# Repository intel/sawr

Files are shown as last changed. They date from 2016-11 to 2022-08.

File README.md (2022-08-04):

DISCONTINUATION OF PROJECT.

This project will no longer be maintained by Intel.

Intel has ceased development and contributions including, but not limited to, maintenance, bug fixes, new releases, or updates, to this project. 

Intel no longer accepts patches to this project.

If you have an ongoing need to use this project, are interested in independently developing it, or would like to maintain patches for the open source software community, please create your own fork of this project. 
Simple Autonomous Wheeled Robot (SAWR)
======================================

The goal of the SAWR project is to define a basic "example robot" to
demonstrate autonomous navigation using [ROS](http://wiki.ros.org/) with
the [Intel&reg; RealSense&trade; 3D cameras][RS]. This robot can also be
used as a software development and testing platform and to deliver training
material.

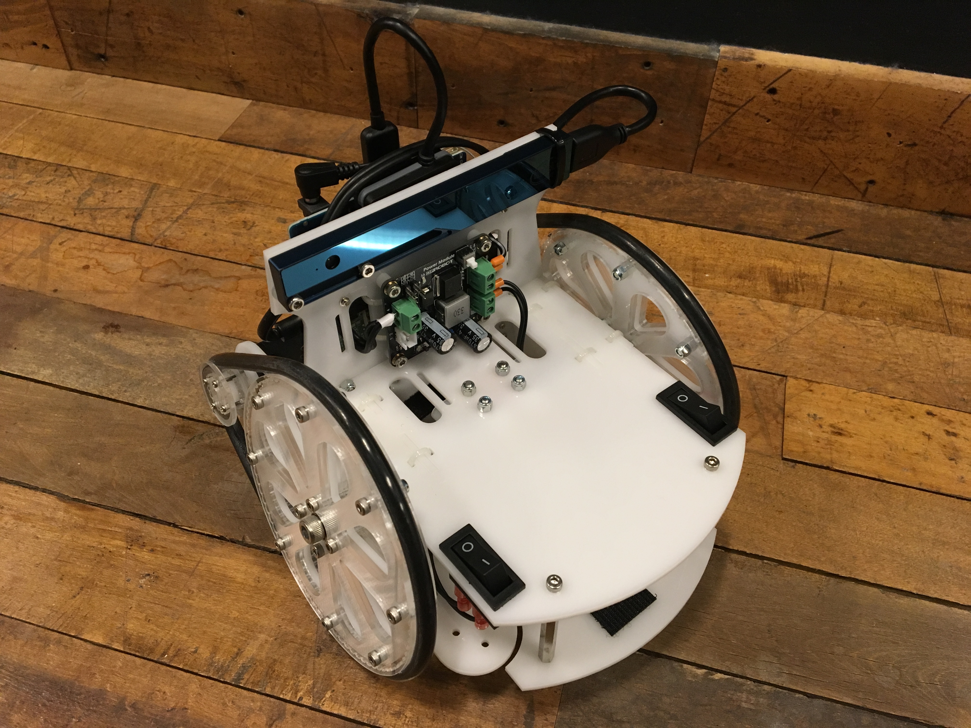
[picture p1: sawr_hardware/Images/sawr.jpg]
SAWR Photo


This repository contains both the hardware specification and the software
to enable you to build, set up, and run your own SAWR.

Hardware
--------
For compute and sensing, you can use either the 
[Intel&reg; RealSense&trade; Robotic Development Kit][RDK]
(which includes an [Aaeon UP Board][UP] and an
[Intel&reg; RealSense&trade; R200 3D camera][R200]) or an
[Intel&reg; Joule&trade; compute module][Joule] an
Intel&reg; RealSense&trade; R200 3D camera.
The frame can also support a [RealSense&trade; ZR300 3D camera][ZR300],
which has additional capabilities for visual odometry and inertial navigation,
but the SW has not yet been fully updated and tested; stay tuned.

The hardware specification, located in [sawr_hardware](sawr_hardware), is
intended to be sufficient to allow you to build your own SAWR if you have
access to a laser cutter.  A general overview of the hardware design is in
[sawr_hardware/README.md](sawr_hardware/README.md) and assembly details are in
[sawr_hardware/ASSEMBLY.md](sawr_hardware/ASSEMBLY.md).

Software
--------
The SAWR software stack enables basic autonomous navigation and currently
supports building a 2D map with gmapper and then planning and executing a
motion path using move-base. It does not yet support out-of-the-box secure
teleoperation, however. You will have to either run ROS over a network
isolated for security, set up a VPN, or set up your own secure remote
teleoperation interface.  See the [Release Notes](RELEASE.md) for details.
Security updates will be distributed via the [Security Notes](SECURITY.md).
If you want to be updated on security issues with the SAWR please 
watch for updates on that file.

The software stack consists of ROS configuration files and some simple ROS 
nodes for motor control. For the most part, we have kept the stack as simple 
as possible. Additional instructions for the SAWR software stack are located 
in the [sawr_master](sawr_master) package:
* [sawr_master/INSTALL.md](sawr_master/INSTALL.md): 
   How to install the SAWR software stack.
* [sawr_master/LAUNCH.md](sawr_master/LAUNCH.md): 
   How to run the SAWR software stack after installation.

Packages
--------
Here is a list of packages included in this project to provide the software
stack for the SAWR and a summary of what each one contains:
* [sawr_master](sawr_master/README.md):
   Master package, installation instructions, and launch scripts.
* [sawr_description](sawr_description/README.md):
   Run-time physical description (URDF files).
* [sawr_base](sawr_base/README.md):
   Motor controller and hardware interfacing.
* [sawr_scan](sawr_scan/README.md):
   Camera configuration.
* [sawr_mapping](sawr_mapping/README.md):
   SLAM configuration.
* [sawr_navigation](sawr_navigation/README.md):
   Move-base configuration.

For the hardware, CAD files and build instructions are located in the 
following package. It is located in the same repository but is not actually 
required for run-time operation:
* [sawr_hardware](sawr_hardware/README.md):
   CAD files and assembly instructions.

Additional Material
-------------------
Please look for the SAWR project under [01.org](https://01.org/sawr)
for links to additional material. Only basic build instructions 
included in this package.  The 01.org site will contain additional
tutorial information including video, as well as a discussion of future
plans.  This site will also act as a hub pointing to any other resources 
(for instance, under the ROS wiki) as they become available.

In particular, we hope to make kits available for purchase and link to them 
from the [01.org SAWR project page](https://01.org/sawr). If you want to make 
and sell a kit, no problem! The licenses used permit commercial use and 
derivatives; see [LICENSES.md](LICENSES.md) for details of the licenses, 
and the package.xml files in each directory for information on which licenses 
apply to each component. However, please do let us know if you are producing 
a kit so we can link to you from the above site.

Contributing
------------
This project welcomes third-party code via GitHub pull requests. Please review 
the [Contribution License Agreement](CLA.md) located in the root of the 
repository. For each pull request submitted, please state your legal name and 
the text, 
> "I agree to the terms of the 'Simple Autonomous Wheeled Robot' (SAWR) CLA."

[RS]: http://www.intel.com/content/www/us/en/architecture-and-technology/realsense-overview.html
[RDK]: https://software.intel.com/en-us/realsense/robotic-development-kit
[UP]: http://www.up-board.org/ 
[R200]: https://software.intel.com/en-us/articles/realsense-r200-camera
[Joule]: https://software.intel.com/en-us/iot/hardware/joule
[ZR300]: https://click.intel.com/intelr-realsensetm-development-kit-featuring-the-zr300.html

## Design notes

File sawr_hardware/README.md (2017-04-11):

Simple Autonomous Wheeled Robot (SAWR) Hardware
===============================================

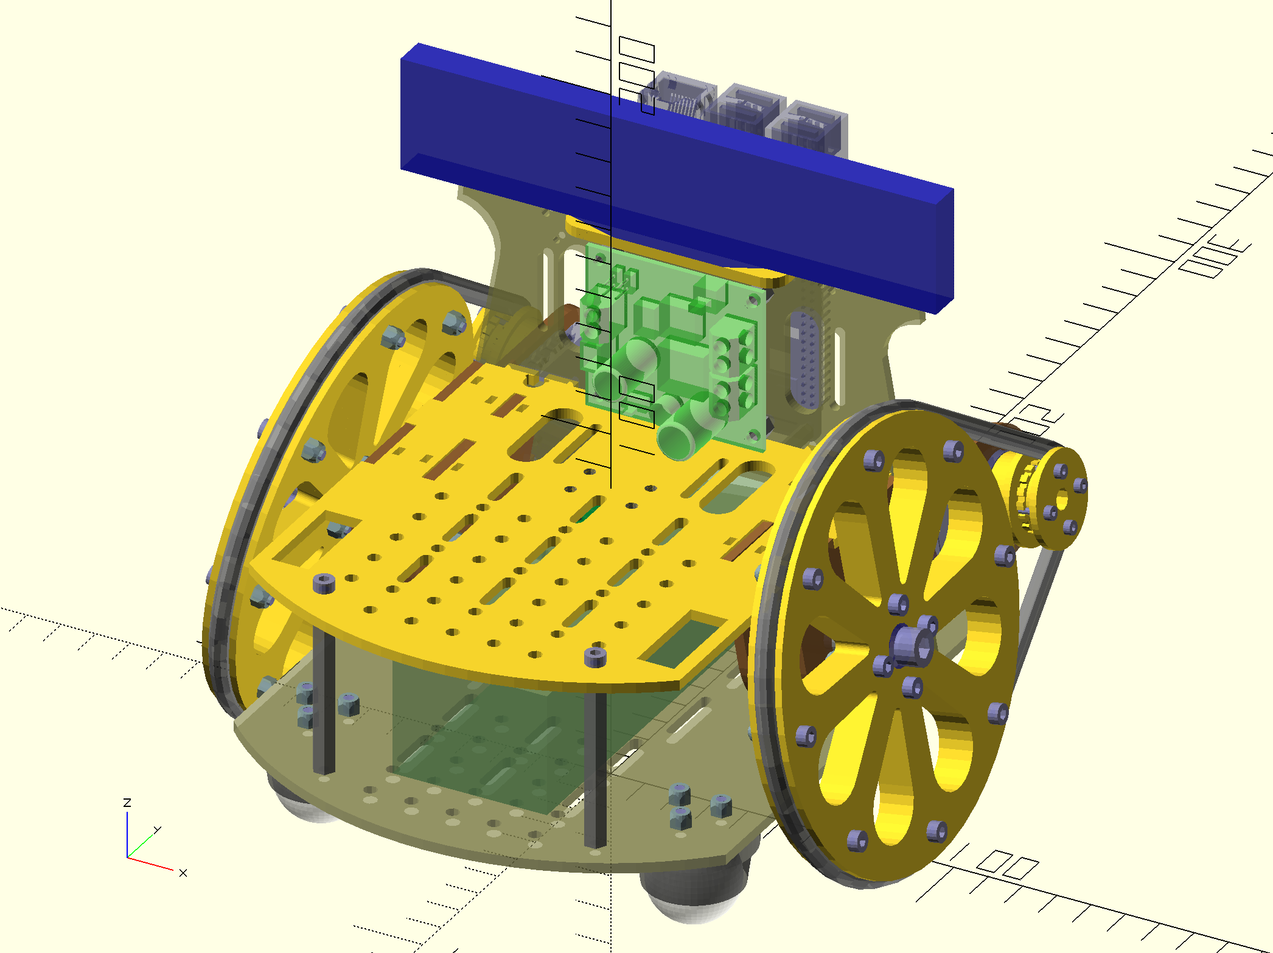
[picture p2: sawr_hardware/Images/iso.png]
OpenSCAD Rendering of SAWR Model


Here is all the information you need to build your own SAWR!

  1. Bills of materials (BOMs) are located under [Materials](Materials). Visit
     the [SAWR project page at 01.org](https://01.org/sawr) to see if kits are
     available. Alternatively you can just source all the parts yourself; links
     are provided to McMaster-Carr and Amazon but other sources can also be
     used as the parts are generally standard.

  2. If you want to cut your own frame, laser-cut files (and 
     [instructions](Make/README.md) on how to use them) are located in the 
     [Make](Make) subdirectory. 

  3. Under the [Models](Models) subdirectory you will find the source CAD
     files. SAWR is modeled using [OpenSCAD](http://www.openscad.org/), an
     open-source 3D parametric modeling system. Using OpenSCAD, models are
     actually described using a textual language, not a direct manipulation
     graphical interface. The main file is `frame.scad`.

  4. Build instructions are located in [ASSEMBLY.md](ASSEMBLY.md).

  5. Further information on the build process, videos, etc will be posted to
     the [SAWR project at 01.org](https://01.org/sawr).

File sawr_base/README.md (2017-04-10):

Simple Autonomous Wheeled Robot (SAWR)
======================================
Base Package
------------

This package provide base system services for the SAWR including:
  1. Control of the Robotis motors via the [Dynamixel SDK][DSDK].
  2. Odometry, by integration of the motor velocities. The code used for this 
     is an elaboration of the [ROS Odometry Setup Tutorial][Odom].
  3. Battery level sensing (using the voltage sensing provided by the motors).

Movement commands should be published as twists on the `cmd_vel` topic and 
odometry will be published on the `odom` topic. An odometry transform is also 
published.

[DSDK]: https://github.com/ROBOTIS-GIT/DynamixelSDK
[Odom]: http://wiki.ros.org/navigation/Tutorials/RobotSetup/Odom

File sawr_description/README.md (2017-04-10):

Simple Autonomous Wheeled Robot (SAWR)
======================================
Description Package
-------------------

This package provide URDF descriptions and models for the SAWR. The master 
files are given in XACRO and the URDF files are generated from them. Launch 
files are provided for publishing this data to the rest of the system. The 
URDF/XACRO model is currently very simple, and is just meant for visualization
and collision detection.

If you are looking for instructions and CAD models to actually build a SAWR, 
look in the [sawr_hardware](../sawr_hardware/README.md) package, where 
you will find a bill of materials (BOM), OpenSCAD files, PDF files for 
laser-cutting a frame, and assembly instructions.

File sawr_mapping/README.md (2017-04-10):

Simple Autonomous Wheeled Robot (SAWR)
======================================
Mapping Package
---------------

This package provide simultaneous mapping and navigation (SLAM).

  1. Mapping is provided by gmapper (which actually only uses a small amount 
     of the data from the camera) to build a 2D map.

  2. Localization is performed using amcl.

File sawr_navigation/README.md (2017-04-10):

Simple Autonomous Wheeled Robot (SAWR)
======================================
Navigation Package
------------------

This package provides navigation.

  1. Move-base is used to maintain obstacle maps and plan and execute routes.

  2. Various parameters need to be tuned if something other than the SAWR is 
     used.

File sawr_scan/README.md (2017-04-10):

Simple Autonomous Wheeled Robot (SAWR)
======================================
Scan Package
------------

This package provides 3D sensing.

  1. RealSense camera nodes are launched.

  2. A LIDAR sensor is simulated by extracting part of the 3D camera data.

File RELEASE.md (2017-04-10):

Simple Autonomous Wheeled Robot (SAWR)
======================================
RELEASE NOTES
-------------

* 2017.04.14: Version 1.0. INITIAL RELEASE
   Basic SW functionality: SLAM with gmapper/amcl, navigation with move-base.
   Motor drivers with odometry.  CAD files and assembly instructions.

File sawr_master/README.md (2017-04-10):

Simple Autonomous Wheeled Robot (SAWR)
======================================
Master Package
--------------

This package serves a few purposes:

  1. To act as a metapackage in that it has dependencies on all other packages
     needed for the SAWR project. In theory, you only have to install this
     package to get all dependencies. In practice, some other manual steps are
     still required to set up your robot, for example to configure your servos,
     and to install software (such as drivers) not available in the ROS 
     package manager or apt repos.

     See [INSTALL.md](INSTALL.md) for details.

  2. Includes launch files for startup. These are organized in "phases" to 
     resolve ordering dependencies. Launch `init_1.launch`, then 
     `init_2.launch`, etc. It is useful to launch each of these in a separate
     window.  Wait for each to stabilize before starting the next. You can
     a lso use the `start.sh` script.   
     
     In fact there are many ways to launch the software system; see
     [LAUNCH.md](LAUNCH.md) for details.

  3. Includes various helper scripts.  For example,

          sudo ./scripts/setperf.sh

     will turn on the performance governor for all cores, which is useful
     on an Intel Joule when using active cooling to push the performance up.

     There are various other scripts in this director useful for testing.
     For example, after launching your basic software stack, try

         ./scripts/viz.sh &
         ./scripts/teleop.sh

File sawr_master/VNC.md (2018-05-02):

TurboVNC
========
[TurboVNC][TurboVNC] is a high performance remote desktop system that also
enables remote 3D graphics. It is based on top of a system called VirtualGL
that supports off-screen 3D rendering via OpenGL pbuffers, tuned compression
mechanisms for 3D content, and a special high-performance JPEG compression
library.

Prerequisites
-------------

### Automatic WiFi Connection

You have to be able to connect via SSH even when not logged in. Unfortunately,
under Ubuntu 16.04, by default WiFi connections set up under a particular user
are dropped when that user logs out.

This can be fixed by editing the connection using the Network Manager (pull
down the network menu at the upper right after establishing a connection to
your WiFi network), selecting Edit on the appropriate connection, and selecting
"All users many connect to this network" under the "General" tab. Also make
sure the "Automatically connect to this network when it is available"
selection is checked.

### System Update

Make sure your system is up to date:
```
sudo apt-get update
sudo apt-get upgrade
sudo apt-get dist-upgrade
```

### Ubuntu MATE (Optional)

Install the Ubuntu MATE Desktop environment for use with VNC to avoid the
overhead of Unity and various issues and bugs when using that environment with
TurboVNC. This is optional but will significantly improve performance.
```
sudo apt-get install mate-desktop-environment \
     mate-dock-applet mate-desktop-environment-extra \
     ubuntu-mate-themes
```

This will need about 600MB of extra storage. After installation, log in using a
normal keyboard and display to initialize the desktop environment. If you do a
first login via VNC, automatic initialization currently has some issues (the panel
crashes) and you may have to do some manual initialization.

Also, you may find when you log into Unity that the theme is a little messed
up: missing icons, strange colors, etc. You can correct this by re-selecting a
theme, such as "Ambient", under the Appearance tab in System Settings.

You can remove the Unity environment afterwards if you wish to get some space
back. BEFORE removing Unity, though, login to MATE and ensure that it is 
configured and that you are comfortable with it.

Here is how you can remove Unity:
```
sudo apt-get purge unity*
sudo apt-get autoremove
```

If you want to reinstall Unity later, you can use:
```
sudo apt-get install unity
```
 
If you chose not to install MATE, you can still run TurboVNC with Unity
but you need to use the `-3dwm` option when starting the server, as Unity
depends on OpenGL to generate various bits of (unnecessary) eye candy.

If you want to remove MATE (again, make sure you have at least one other
display manager installed and working...) use
```
sudo apt-get purge mate-desktop-environment-core
sudo apt-get purge mate-desktop-environment-extra
sudo apt-get autoremove
```

Setup
-----
Follow the [instructions to set up a TurboVNC server][TurboVNC_UG],
a summary of which, appropriate for Ubuntu 16.04, is given below. 

Download 
[`libjpeg-turbo-official_1.5.1_amd64.deb`][TurboJPEG_deb],
[`virtualgl_2.5.2_amd64.deb`][VGL_deb], and 
[`turbovnc_2.1.1_amd64.deb`][TurboVNC_deb] from the corresponding
SourceForge download sites. Later versions should also work.

Install these packages as follows; note you need to remove any previous 
installation of VirtualGL first. It's ok to run the removal command to
check even if there isn't a previous installation.
```
sudo dpkg -i libjpeg-turbo-official_1.5.1_amd64.deb
sudo dpkg -r virtualgl
sudo dpkg -i virtualgl_2.5.2_amd64.deb
sudo dpkg -i turbovnc_2.1.1_amd64.deb
```

You may want to add `/opt/TurboVNC/bin` to your path. If so, add the
following to your `.bashrc`:
```
export PATH=/opt/TurboVNC/bin:$PATH
```
The following doesn't assume you've done this, though.

After doing the above, log out, and log back in remotely using SSH 
```
ssh {user}@{host}
```

Temporarily shut down the display manager:
```
sudo service lightdm stop
```
If you still have a screen attached to the target computer, it should go
black at this point.

Run the VirtualGL configuration program:
```
sudo vglserver_config
```
select option 1, accept all the suggested configuration defaults, then
use X to exit.

Restart the display manager:
```
sudo service lightdm start
```

Add any user who will use TurboVNC to the `vglusers` group.  In the 
following we assume there is only going to be one TurboVNC user, 
and that this is the current user:
```
sudo usermod -a -G vglusers $USER
```

Also add root to the `vglusers` group:
```
sudo usermod -a -G vglusers root
```

Log out and log back in and confirm that you are part of the `vglusers`
group using
```
groups
```

Manually Starting TurboVNC
--------------------------
Login remotely to the computer using SSH. Replace `{host}` with the name or
IP address of the target computer, and `{user}` with an appropriate username.
```
ssh {user}@{host}
```

Start a TurboVNC server. After it starts, it will give you a display number to
use (typically `:1`).  In the following we will refer to this as `:{n}`.
```
/opt/TurboVNC/bin/vncserver
```

NOTE: the above is for Ubuntu MATE.  If you are running the stock Unity 
display manager (_not_ recommended for performance reasons...) then you will
have to use the following instead:
```
/opt/TurboVNC/bin/vncserver -3dwm
```
The _GOOD_ news of doing this though is that since everything is considered to
be 3D capable, you don't need to prefix applications with `vglrun`.  The bad
news is that everything will be considered 3D and will use more resources than
necessary.

If this is the first time you have used it, TurboVNC may prompt for an 8-character
password. Note that this provides only minimal security, and in particular the
datastream will be unencrypted. If you want better security, using an SSH
tunnel is recommended (see below).

Now back on the client machine, start a viewer on the appropriate host and
display number. If you are on a Linux machine in which you have also installed
TurboVNC, you can use
```
/opt/TurboVNC/bin/vncviewer
```

The viewer may complain about not being able to find a Java runtime. If it
does, install OpenJDK-8 as follows (_not_ 9; TurboVNC does not currently support
version 9):
```
sudo apt-get install openjdk-8-jdk
```

Once you start the viewer successfully it will open a window and prompt for a
server. Enter the hostname or IP, followed by a colon and the display number,
as follows: `{host}:{n}`. The viewer will then prompt for the password you set
in the previous step.

You should now see a desktop. However 3D applications, if run in the usual
way, will complain that there is no OpenGL support. You have to grant access to
OpenGL for each 3D application using the `vglrun` prefix command. For example,
suppose we want to run OpenSCAD, a 3D CAD program. We would need to use the
following:
```
/opt/VirtualGL/bin/vglrun openscad
```
Alternatively, if you have a RealSense camera and librealsense installed,
you can try these:
```
/opt/VirtualGL/bin/vglrun cpp-pointcloud
/opt/VirtualGL/bin/vglrun cpp-capture
```
This also works:
```
/opt/VirtualGL/bin/vglrun roslaunch sawr_navigation display.launch &
```
or even this:
```
/opt/VirtualGL/bin/vglrun rosrun sawr_master/scripts viz.sh
```

The `vglrun` prefix command has [various options][VGLrun]. One nice thing about 
`vglrun` though is that all processes started recursively by the target command
are also 3D enabled. So for instance, as shown in the examples above, you can use
`vglrun` on scripts that start multiple other 3D things, or start terminals that
start 3D things, or use `rosrun` or `roslaunch` that launch other programs that
(eventually) start a process that actually needs 3D. Of course this may start
things that don't need 3D, so you should still be a _little_ selective.

Stopping a Manually Started VNC Server
--------------------------------------
After logging out, stop the TurboVNC server via the SSH shell to the remote
machine using
```
/opt/TurboVNC/bin/vncserver -kill :{n}
```

If you want, you can also list all current sessions:
```
/opt/TurboVNC/bin/vncserver -list
```

Using SSH Tunneling
-------------------
_NOTE: This part of the instructions is still under development. In particular,
TurboVNC has some built-in options for SSH tunnelling that may make setting up
your own tunnel unnecessary._

If you are on an insecure network (for instance, a wireless network) and want
improved security, you can set up SSH tunneling. You can set up a tunnel using
SSH as follows:
```
ssh -L {localport}:localhost:{remoteport} {user}@{host}
```

For example, if the VNC server is running on display `:1`, as it usually the
case, then it will use port 5901. Use a different port locally to avoid any
conflicts with local VNC servers, such as 15901:
```
ssh -L 15901:localhost:5901 {user}@{host}
```

Now follow the steps above to start the remote server. The SSH session to set
up the port forwarding can also be used to start the remote VNC server
manually.

The only difference is that now you need to start the local viewer as follows:
```
/opt/TurboVNC/bin/vncviewer localhost:1::15901
```
and it won't prompt for a server or display.

If you are using another VNC client, such as tightvnc or Remmina, you can use
`localhost:15901` whenever it prompts for the server.

Tuning Performance
------------------
You can adjust the quality settings in the preferences of the TurboVNC viewer
to improve performance. Lowering the quality setting improves both uses less
bandwidth and reduces computation time. Try 4X chromatic subsampling in
particular.

To improve network performance, try to put as many nodes as possible on a wired
network. For instance, even if you have a robot that _needs_ to be wireless,
connect the laptop or computer controlling it directly to the access point with
a wired connection if possible. This can significantly reduce latency.

If you are not using Ubuntu MATE, you can also improve performance by switching to
it. In testing, MATE used roughly half the CPU of Unity on a Joule.

[TurboJPEG_deb]: https://sourceforge.net/projects/libjpeg-turbo/files/1.5.1/libjpeg-turbo-official_1.5.1_amd64.deb/download
[VGL_deb]: https://sourceforge.net/projects/virtualgl/files/2.5.2/virtualgl_2.5.2_amd64.deb
[TurboVNC_deb]: https://sourceforge.net/projects/turbovnc/files/2.1.1/turbovnc_2.1.1_amd64.deb
[TurboVNC]: http://www.turbovnc.org/
[TurboVNC_UG]: http://www.virtualgl.org/vgldoc/2_1_1/
[VGLrun]: http://www.virtualgl.org/vgldoc/2_1_1/#Advanced_Configuration

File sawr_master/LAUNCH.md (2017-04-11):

Simple Autonomous Wheeled Robot (SAWR)
======================================
Launching the Software Stack
------------------------

The SAWR software stack supports autonomous navigation using simultaneous 
localization and mapping (SLAM). This means that it is capable of creating a 
model of its environment (a map) and then figuring out its current location 
with respect to that map (localization). In addition, autonomous navigation 
is supported. This means the robot can be given a goal destination in the map,
then it can plan a path from its current estimated position to the destination,
and then execute the plan. The plan of course will route around known obstacles
in the map but during execution the robot will also dynamically avoid obstacles
that show up along the way, re-planning as necessary.

How Robot Navigation Works

This is a complex system but is the basis of many other applications in mobile
robotics. To manage complexity, the software system is built up from a number
of phases or "layers". 

* The first layer just supports control of the motors,
  allowing the robot to move forward and turn with specific velocities, and to
  estimate actual progress using odometry. 
* The second layer enables the Intel&reg; RealSense&trade; 3D cameras and
  generates data that simulates a LIDAR.
* The third layer takes this data and implements SLAM, building a map and
  localizing.
* The fourth layer does planning and navigation.

Finally, to control the robot and see where it is, we can use a visualization
tool to observe the map and give the robot navigation goals, and can also
use "teleoperation" to directly drive the robot from place to place.

The layers are built up from standard ROS nodes for SLAM and navigation.
In particular, we use the [ROS Kinetic Kame](http://wiki.ros.org/kinetic)
release, the ROS [slam_gmapping](http://wiki.ros.org/slam_gmapping) package
for mapping, [amcl](http://wiki.ros.org/amcl) package for probablistic
localization, and the ROS [move-base](http://wiki.ros.org/move_base) package
for navigation.  This is similar to the stack used in the 
[ROS navigation](http://wiki.ros.org/navigation) package.

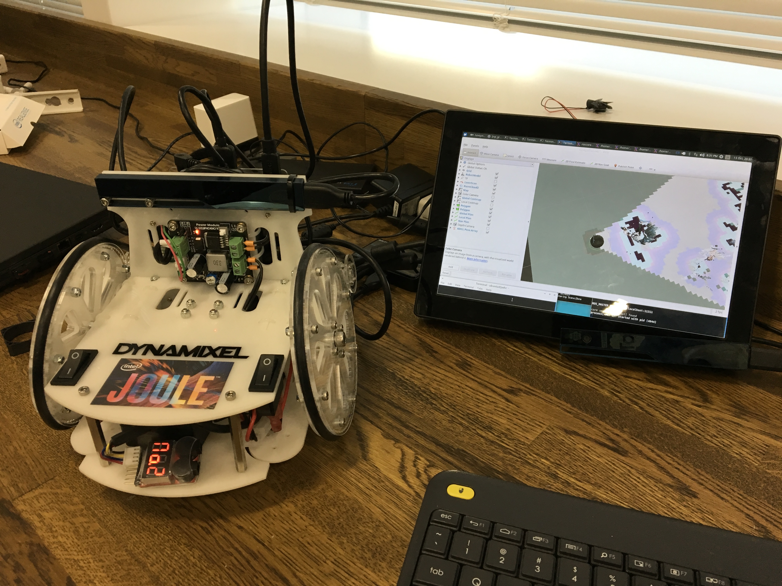
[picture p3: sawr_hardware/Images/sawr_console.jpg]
SAWR Running Navigation Stack


The SAWR software stack can be launched in a number of different ways,
depending on your situation. In theory you could start all the ROS nodes used 
using a single launch file. In practice, this sometimes does not work due to
race conditions in some of the nodes. So instead it is recommended to launch
the SW stack in phases, each phase adding another software layer with a bit
more functionality.

Breaking the launch process into phases is also useful if you want to
experiment with alternative "higher" layers (like an alternative SLAM stack)
while leaving the "lower" layers (like motor control) alone, or just want to
test the robot bringup incrementally.

Here are the various ways to start the system.

Script-Driven Under X11
-----------------------

If you are running using X11, either locally (eg with an HDMI cable tether)
or over the network with `ssh -X`, you can run the `start.sh` script.
This launches all the "phases" with the output redirected to an xterm,
one xterm per phase, and with a delay between each phase to avoid race
conditions.

The xterms allow you to monitor the output of each phase
in real time, but be aware that if the xterms are terminated those
nodes will close (and also, if the nodes crash, the xterms will close).
This approach is useful for testing but perhaps not for a final install.

To take this approach, issue the following commands, either from the main 
X11 display or over an X-tunnelled ssh session:
    
    roscd sawr_master
    ./start.sh

Script-Driven Without X11
-------------------------

If you want to launch the entire software stack without starting xterms,
you can use the `nox_start.sh` script. The same approach will be taken with
delays between phases as above, but output will be directed to the ROS logs.
This is useful if you are logging in remotely with just a shell script
but no remote X11 server, or if you want to avoid a dependency on keeping
the xterms running.

To take this approach, issue the following commands. You can do this
remotely using a regular ssh session (without X11 tunnelling):
    
    roscd sawr_master
    ./nox_start.sh

Launching Phases Manually
-------------------------

Sometimes you want to test phases separately if you are doing debugging.
You can launch a phases yourself manually using

    roslaunch sawr_master init_X.launch

With X one of 0, 1, 2, or 3.  If you want, launch these in separate terminals
or ssh sessions to see the output.  Note that you do not have to be in 
the ``sawr_master`` directory.

Note: all phases need to share a single `roscore` instance.  You can start
this separately, but it is also started automatically by `roslaunch` if
it is not already running.  The above scripts start it automatically.

Launch Everything at Once
-------------------------

This launches all the phases at the same time without delays in between.
For the reasons noted above, this might not work (it is known not to under
ROS Indigo) but (if certain issues in ROS or the nodes are resolved over time)
may work on your installation. If you want to, you can try simultaneous launch
using:

    roslaunch sawr_master init.launch

Note this does not use a script but just ROS tools.  You do not have to be in
the `sawr_master` directory.

Teleop and Visualization
------------------------
Now that the software stack is launched, you can "drive" the robot using a
teleoperator and visualize the progress of SLAM (eg generation of a map) with
rviz.

Do the following in two separate windows:

    roslaunch sawr_navigation display.launch
    rosrun teleop_twist_keyboard teleop_twist_keyboard.py

You can also launch these using scripts:

    roscd sawr_master
    ./scripts/viz.sh &
    ./scripts/teleop.sh

Manual Navigation
-----------------
Once you have a teleop running and a visualization, you can drive the robot
around manually and build up a map.  You can observe the map being updated
dynamically in rviz. Once you have a good map for a particular environment
you can [save it](http://wiki.ros.org/map_server) using the `map_saver` 
command to the map server, and then using the `start_saved.sh` script
provided, restart the system with that map. Upon restart with a saved map,
the robot will immediately try to localize itself against the map to
determine its initial position.

Autonomous Navigation
---------------------
Once you have a map and the robot has localized itself against the map,
you can try autonomous navigation. This is done by specifying a goal position
and orientation. Technically this is done by sending a message to the 
`move-base` sub-system which initiates a ROS navigation "action" (an "action"
is long-running process in ROS that you can observe the progress of, cancel, 
etc.). Actions are particularly appropriate for navigation, but also useful
in many other kinds of autonomous tasks.

It is possible to initiate a navigation action using rviz. Once you have a map
displayed and the robot has localized, select the "Set Goal" button at the top
of rviz, then click on a point on the map, drag a bit to select the 
orientation, and release the button. Rviz will then post the goal, and,
if all goes well... your robot will autonomously navigate to the goal 
position and orientation, avoiding obstacles on the way.

Remote Access
-------------
The above can be done using a HDMI cable and keyboard connected to the robot
but this is obviously not very satisfactory.  Instead we want to be able to
control the robot remotely and have it run untethered.
 
If you set up remote access via ssh as noted in [INSTALL.md](INSTALL.md),
you will be able to launch the software stack remotely.  If you use 
`ssh -X` to access the system over the internet, even the X11 versions with 
multiple terminal windows will work---definitely on a remote Linux or MacOS 
system but even from Windows if you install an X server such as 
[Xming](http://www.straightrunning.com/XmingNotes/).

Unfortunately rviz will not work remotely over X11, so to use it remotely
you will have to either set up remote ROS access (which will be insecure
unless you also set up a VPN like OpenVPN) or set up a VNC server on your
robot (less efficient, but VNC can be tunnelled over ssh).

You can also give goal states for navigation using command line tools, but
you would have to figure out the coordinate system the robot uses for its map.

See the security discussion in the [INSTALL.md](INSTALL.md) file to set up
remote access.  Doing this securely on a public network is unfortunately
difficult so you may want to start with a private WiFi network (eg behind an
external firewall).

Launching Automatically at Boot
-------------------------------
The simplest way to launch the system automatically at boot is to enable
automatic login and then configure it as a 
[Startup Application](https://help.ubuntu.com/16.04/ubuntu-help/startup-applications.html).
Note that you may have to run it inside a terminal window to get this to work.
This is somewhat insecure, as someone could in theory plug in a keyboard, 
mouse, and monitor to your robot and access your account, but you can always
have your login time out quickly.  However, since anyone with physical access
to your robot can typically break in without too much trouble anyway even if
you don't set up automatic login...

You can also configure a [script to run at boot using systemd](https://linuxconfig.org/how-to-automatically-execute-shell-script-at-startup-boot-on-systemd-linux).
This is a bit more robust and will work even without automatic login, and 
even if you disable the windowing system, but is a little harder to set up.

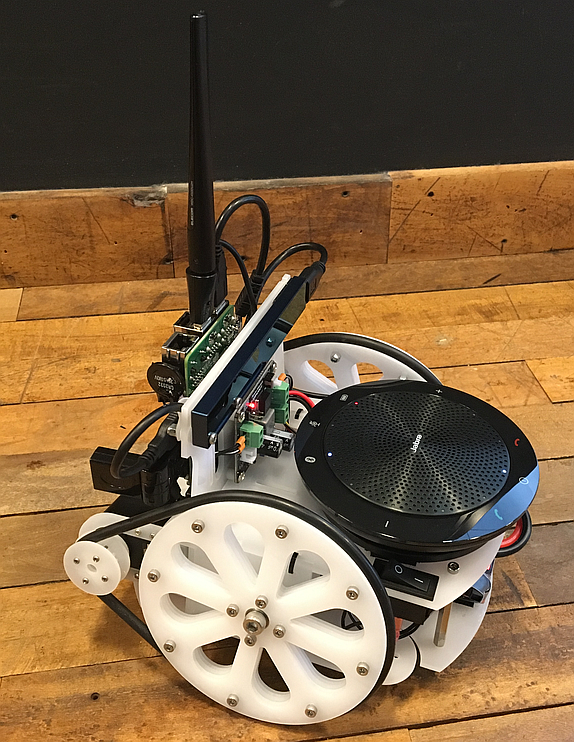
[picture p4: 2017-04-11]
sawr_hardware/Images/sawr_audio.png

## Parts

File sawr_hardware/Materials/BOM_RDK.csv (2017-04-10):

 | SAWR with Laser Cut Components for Intel® RealSense(TM) Robotic Development Kit
 | Note : prices are from online retailers and for reference only.
Section | Part | Link | Estimated cost per bulk pkg | Qtty of parts in bulk pkg | Qtty per unit required | Estimated cost per unit | Notes
Frame | Laser cutting |  | $2.50 | 1 | 30 | $75.00 | It takes about 30 minutes to cut. Pololu charges $2.50 per minute of cutting time.
$91.60 | Acrylic sheet 450mm x 300mm x 2mm |  | $4.75 | 1 | 1 | $4.75 | Estimated cost of materials (POM/Acetal can be used instead)
 | Acrylic sheet 450mm x 300mm x 3mm |  | $7.90 | 1 | 1 | $7.90 | Estimated cost of materials (POM/Acetal can be used instead)
 | Pololu 1" ball caster with plastic rollers (1 at least; 2 additional as option) | https://www.pololu.com/product/2691 | $3.95 | 1 | 1 | $3.95 | 1 ea used in current design; 2 more can be added for extra stability.
Electronics | Intel RealSense Robotic Development Kit | http://click.intel.com/intelr-realsensetm-robotic-development-kit-2054.html | $349.00 | 1 | 1 | $349.00 | Estimated cost.
$553.20 | DFRobot DC-DC 5A power convertor | http://www.dfrobot.com/index.php?route=product/product&path=70_119&product_id=752#.VpaHJ1LtvT9 | $8.50 | 1 | 1 | $8.50
 | Robotis MX-12W Dynamixel servos | http://www.trossenrobotics.com/dynamixel-mx-12w-robot-actuator | $65.90 | 1 | 2 | $131.80 | Get individual boxes; additional parts (brackets, bolts) included and needed for build! | you need the included mounting brackets if you laser-cut the frame.
 | (Alternative source for servos) | http://www.robotis.us/dynamixel-mx-12w/ |  | 1 | 0 | $- | Alternative source for servos
 | USB2AX v3.2a (Servo interface) | http://www.trossenrobotics.com/usb2ax | $39.95 | 1 | 1 | $39.95
 | TP-LINK AC600 High Gain Wireless Dual Band USB Adapter | https://www.amazon.com/TP-LINK-Wireless-Adapter-Archer-T2UH/dp/B00UZRVY12 | $23.95 | 1 | 1 | $23.95 | AC mode and 5GHz support recommended, but less expensive b/g/n model can be used. Also tested with CanaKit WiFi dongle; many other options.
Electrical harness and cables | Battery (LiPo 3S, 3000mAh to 4000mAh) | https://www.amazon.com/Venom-4000mAh-Battery-Universal-Traxxas/dp/B000W7WWFW?s=toys-and-games | $41.91 | 1 | 1 | $41.91 | Has adapters for many different connectors. Alternative: Turnigy 5000mAh 3S 20C Lipo Pack, but has X-60 connector.
$56.10 | Lipo Battery Monitor/Alarm | http://www.amazon.com/Battery-Tester-Voltage-Buzzer-Alarm/dp/B005GJCJOA | $2.96 | 1 | 1 | $2.96 | Gives audible alarm if battery gets too low, allows monitoring of individual cells.
 | Tamiya Male and Female Plug Set M/F 150mm by Venom | https://www.amazon.com/Tamiya-Male-Female-150mm-Venom/dp/B000HKEVH6 | $3.99 | 1 | 1 | $3.99 | Depending on Battery connector this may not required.
 | Barrel connector Adapter 10 Pack | https://www.amazon.com/iMBAPrice-iMBA-CCTV-PGTM-10-Security-Camera-Pigtail/dp/B0054D80LE | $5.99 | 10 | 1 | $0.60 | 1-UP board
 | 120 Assorted Fuses / 10 Inline Fuse Holders - Includes Puller | https://www.amazon.com/Assorted-Fuses-Inline-Fuse-Holders/dp/B01E5MM63C?s=automotive | $15.99 | 10 | 1 | $1.60 | For price reference only. Auto kit, can be substituted with inline fuse holder and 5A glass fuse. Recommended wire gauge not less than 22 AWG. Ferrules specified below should correspond to this wire gauge.
 | On/Off Rocker switch pack of 5 | http://www.amazon.com/SPST-Black-Snap-Rocker-Switch/dp/B008X10YRC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 | $4.17 | 5 | 2 | $1.67 | One switch for motors, other for main switch.
 | Female insulated crimp spade disconnects 100 pc | https://www.amazon.com/Haobase-100pcs-Fully-Insulated-Disconnects-Terminal/dp/B01BHQI7U0 | $5.99 | 100 | 4 | $0.24 | For secure but removable switch connections
 | Ferrules, 22AWG 100 pcs | http://www.amazon.com/gp/product/B00GPH555C?refRID=B5R7Y431MTX1X1HTPKSG&ref_=pd_ys_c_rfy_rp_3 | $4.19 | 100 | 6 | $0.25 | Optional, but provide secure connections to screw terminals. Orange
 | 200mm Dynamixel cables pack of 10 | http://www.trossenrobotics.com/p/200mm-3-pin-dynamixel-compatible-cables-10-pack | $13.90 | 10 | 1 | $1.39
 | 250mm Dynamixel cables | http://www.trossenrobotics.com/p/250mm-3-pin-dynamixel-compatible-cables-10-pack | $14.90 | 10 | 1 | $1.49
 | 100 mm Dynamixel cable |  |  |  | 1 |  | Part of Dynamixel servos, when individual boxes selected.
Hardware | Velcro tape, sticky back pack of 10 | https://www.amazon.com/VELCRO-Brand-Sticky-Strips-Clear/dp/B00168A18G?s=electronics | $2.09 | 4 | 0.5 | $0.26 | For mounting battery monitor/alarm.
$48.67 | Velcro straps for the battery pack of 50 | http://www.amazon.com/Reusable-Fastening-Velcro-Cable-Microfiber/ | $9.98 | 50 | 4 | $0.80
 | 4-Inch Cable Ties - 100 Pack | https://www.amazon.com/C2G-Cables-43036-4-Inch-Cable/dp/B0002GX1XA | $2.59 | 100 | 15 | $0.39 | Attach camera to tower plate, sides to top and bottom plates. Check length: min 100mm, width = max 4mm, should be flexible.
 | 9464K161 Chemical-Resistant Multipurpose O-Ring | http://www.mcmaster.com/#9464k161/=14o4emp | 3.97 | 1 | 2 | $7.94 | 2-Wheels
 | 92095A168 Button-Head M3x14 | http://www.mcmaster.com/#92095a168/=138tce6 | $5.80 | 50 | 24 | $2.78 | 24-Wheels
 | 90576A102 Nylon-Insert Locknut M3 | http://www.mcmaster.com/#90576a102/=12xtc3z | $3.27 | 100 | 37 | $1.21 | 24-Wheel, 4-frame, 3-casters, 2-RS, 4-DF-Robot; get 6 more if add 2 optional casters
 | 92080A033Zinc-Plated Brass Female Threaded Hex Standoff M3x51 (6.3mm thread) | http://www.mcmaster.com/#95947a075/=12xtho2 | $2.91 | 1 | 2 | $5.82 | 51 mm (no 50mm on McMaster), thread length 6.3mm - good for M3x8 screw. 2-base
 | 91292A111 Socket Head Cap Screw M3x6 | http://www.mcmaster.com/#91292a111/=12xtjlw | $8.56 | 100 | 4 | $0.34 | 2- base to tower, 2- top to tower
 | 94500A222 Button-Head Screw M3x8 | http://www.mcmaster.com/#94500a222/=12xtm3r | $5.77 | 100 | 7 | $0.40 | 3-casters get 6 more if using 2 additional casters), 4-front standoffs
 | 91292A029 Socket Head Screw M3x18 | http://www.mcmaster.com/#91292a029/=13a8dhv | $5.60 | 100 | 2 | $0.11 | 2-camera to tower (head 5.5mm dia fits in slot on RS)
 | 95947A011 Aluminum Female Full Threaded Hex Standoff 2.5x16 | http://www.mcmaster.com/#95947a011/=140th7h | $0.70 | 1 | 4 | $2.80 | 4-UP Board
 | 90128A183 Cap head 2.5x6 screws | http://www.mcmaster.com/#90128a183/=139q9z0 | $7.70 | 100 | 8 | $0.62 | 8-UP Board
 | 93295A094 Brass Unthreaded Spacer M3x6 mm | http://www.mcmaster.com/#93295a094/=140typ2 | $0.49 | 1 | 4 | $1.96 | 4-DFRobot
 | 92005A124 Metric Pan Head Phillips Machine Screw M3x14 | http://www.mcmaster.com/#92005a124/=140u2lr | $4.24 | 100 | 4 | $0.17 | 4-DFRobot
 | 92000A015 Pan Head Phillips Screw M2x8 | http://www.mcmaster.com/#92000a015/=140t8vj | $4.52 | 100 | 28 | $1.27 | 12-brackets to tower, 16- servo side mount
 | 93625A101 Nylon-Insert Locknut M2 | http://www.mcmaster.com/#93625a101/=12xu5kl | $6.82 | 10 | 12 | $8.18 | 12-brackets to tower. Not needed if get individual boxed servos.
 | 95610A530 Nylon Flat Washer M3x 1mm | http://www.mcmaster.com/#95610a530/=135yg98 | $2.84 | 100 | 10 | $0.28 | 6-camera to tower spacers (3ea for each screw), 2 -base to tower screws, 2-top to tower screws
 | 92981A106 Alloy Steel Shoulder Screw | http://www.mcmaster.com/#92981a106/=138tvan | $1.30 | 1 | 2 | $2.60 | 2 Wheel axle shoulder screw 40mm-shoulder, 10mm-M5 thread (alternative: can use 6mm screw with unthreaded section at least 12mm long)
 | 97725A600 Metal Sealing Washer 9.9 mm dia | http://www.mcmaster.com/#97725a600/=138tyo9 | $9.88 | 50 | 10 | $1.98 | 6-to expand 6mm spacer between wheel and mount, 4-between mount and 14 mm spacer
 | 94669A169 6mm spacer ID=6.3mm | http://www.mcmaster.com/#94669a169/=139qmrc | $0.66 | 1 | 2 | $1.32 | 2-outside spacer between wheel and mount
 | 90576A104 M5 Steel Nylon-Insert Locknut | http://www.mcmaster.com/#90576a104/=138uvlh | $4.27 | 100 | 2 | $0.09 | 2-secure axle bolt on inner mount plate. Will need 8mm wrench to secure this nut.
 | 94669A181 M6x14mm Unthreaded Spacer | http://www.mcmaster.com/#94669a181/=139qq8x | $0.93 | 1 | 2 | $1.86 | 2-between mount plates.
 | 91290A049 M2x20 Socket Head Cap Screw | http://www.mcmaster.com/#91290a049/=138vb62 | $11.16 | 100 | 8 | $0.89 | 8-driver to servo hub
 | 7804K112 Stainless Steel Ball Bearing | http://www.mcmaster.com/#7804k112/=13coawe | $7.67 | 1 | 0 | $- | 4-wheels. Alternative source in US
 | Powers PJ-BB1260ZZ bearing pack of 10 | https://www.amazon.co.jp/Powers-PJ-BB1260ZZ-%E3%83%91%E3%83%AF%E3%83%BC%E3%82%BA%E3%83%99%E3%82%A2%E3%83%AA%E3%83%B3%E3%82%B0-1260%E3%82%B5%E3%82%A4%E3%82%BA-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 | $11.08 | 10 | 4 | $4.43 | 4-wheel. source for metric bearings in JPN
 | Cable organizer clip | https://www.amazon.com/Jiewei-Adhesive-Cable-Holder-Organizer/dp/B01DIIRIAA | $7.99 | 100 | 2 | $0.16 | Sticky clip helps to organize wires
Tools Needed | 8mm wrench (for axle nut) |  |  |  |  |  | To secure axle nut
 | Allen wrench 1.5mm hex |  |  |  |  |  | Drivers' scews
 | Allen wrench 2 mm hex |  |  |  |  |  | Other hex screws
 | Allen wrench 3 mm hex |  |  |  |  |  | To secure axle screw
 | Philips #1 screwdriver |  |  |  |  |  | Other Philips screws
 | Crimper for ferrules
 | Crimper for spade disconnects
 | Wire cutter |  |  |  | Per Robot | $749.56
 |  |  |  |  | # of components | 259.5

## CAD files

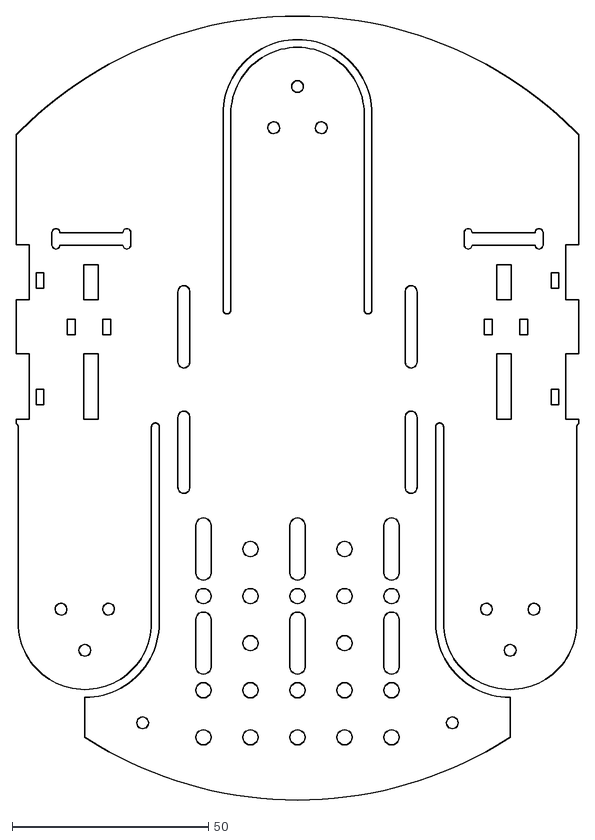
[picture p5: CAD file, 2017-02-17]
sawr_hardware/Parts/base_accessory.dxf
143.4 x 200.0

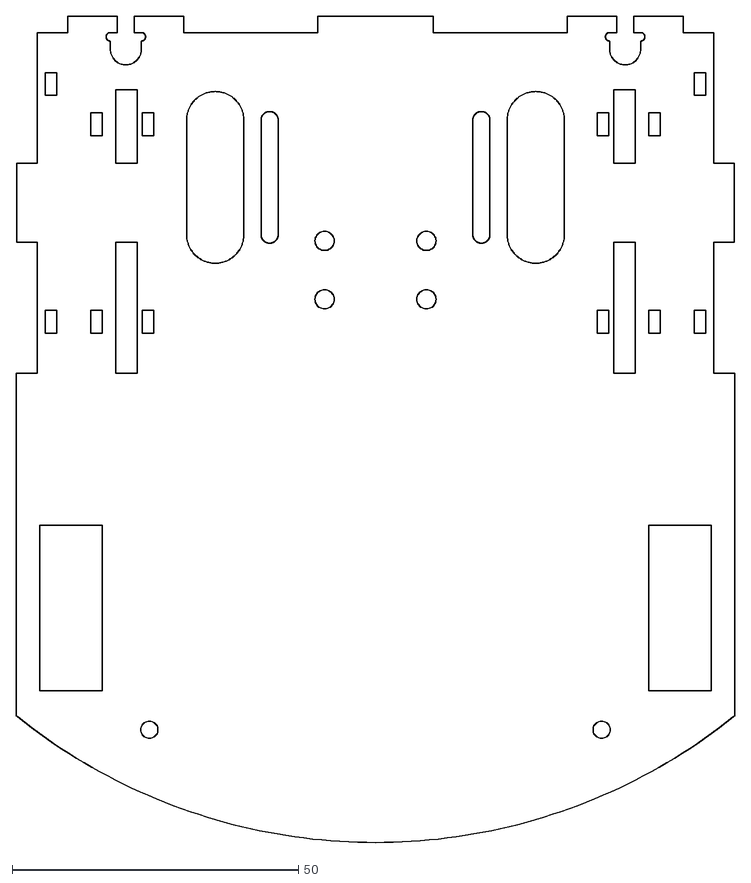
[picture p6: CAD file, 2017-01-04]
sawr_hardware/Parts/top.dxf
125.5 x 144.3

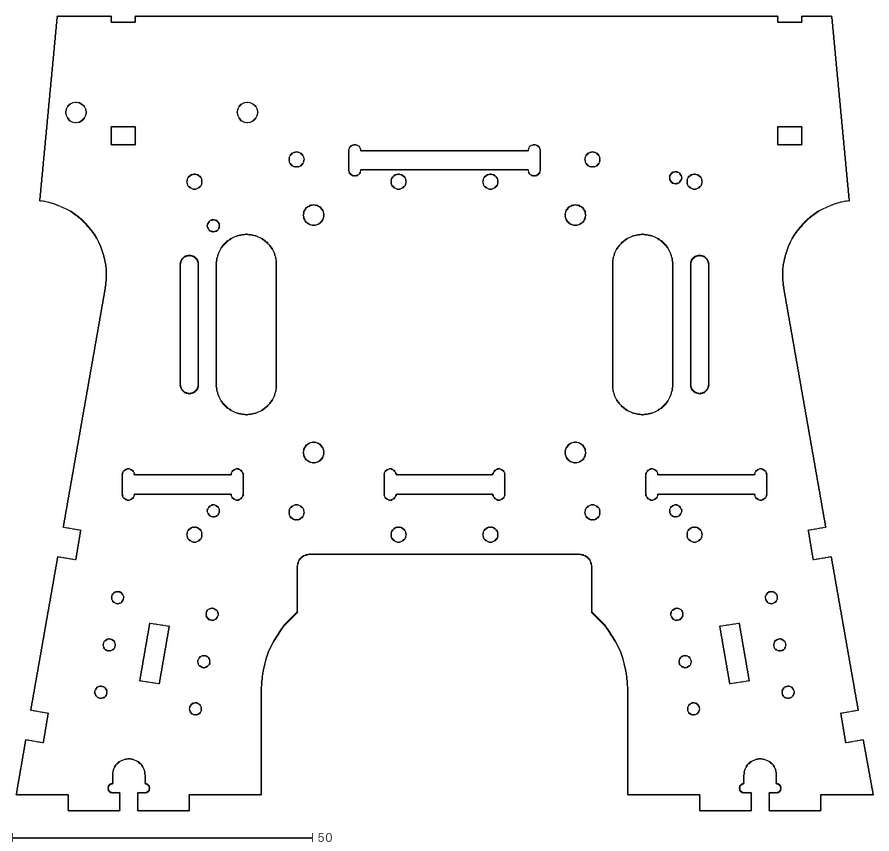
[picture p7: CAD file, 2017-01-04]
sawr_hardware/Parts/tower.dxf
142.8 x 132.4

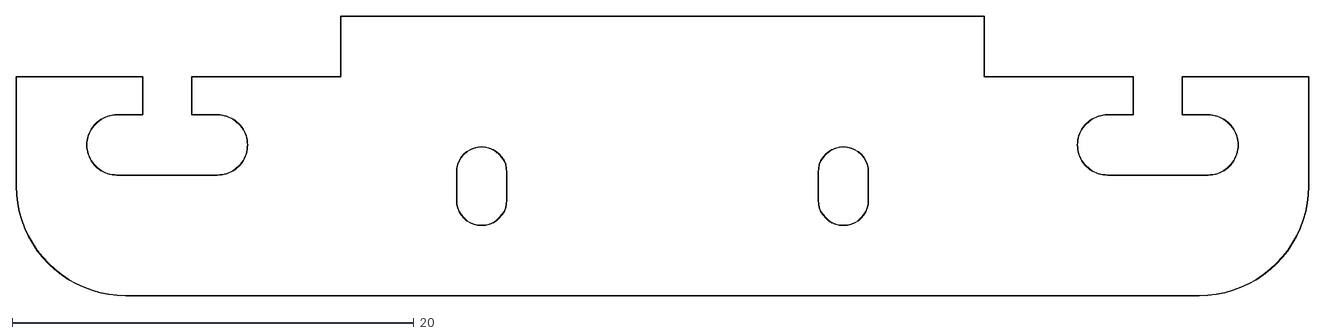
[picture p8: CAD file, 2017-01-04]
sawr_hardware/Parts/shelf.dxf
64.3 x 13.9

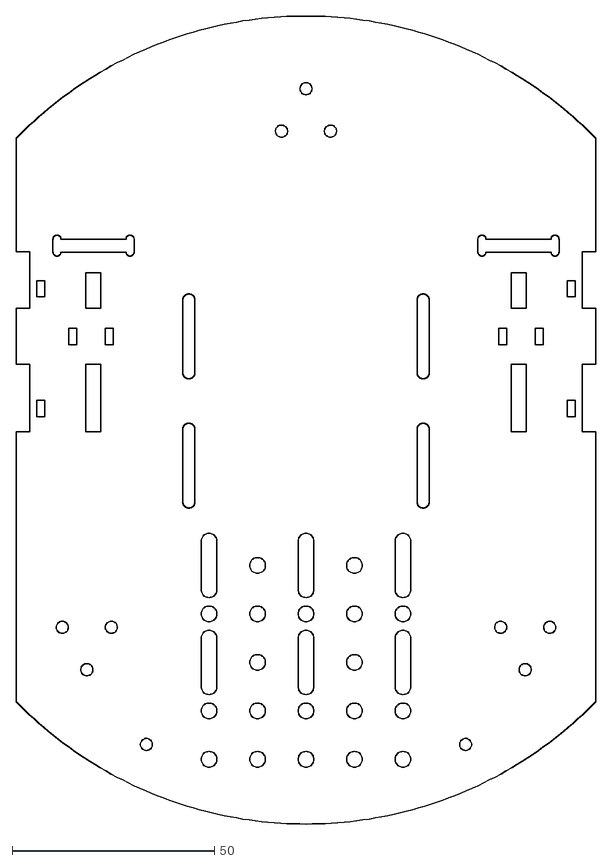
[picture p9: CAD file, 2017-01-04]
sawr_hardware/Parts/simple_base_accessory.dxf
143.4 x 200.0

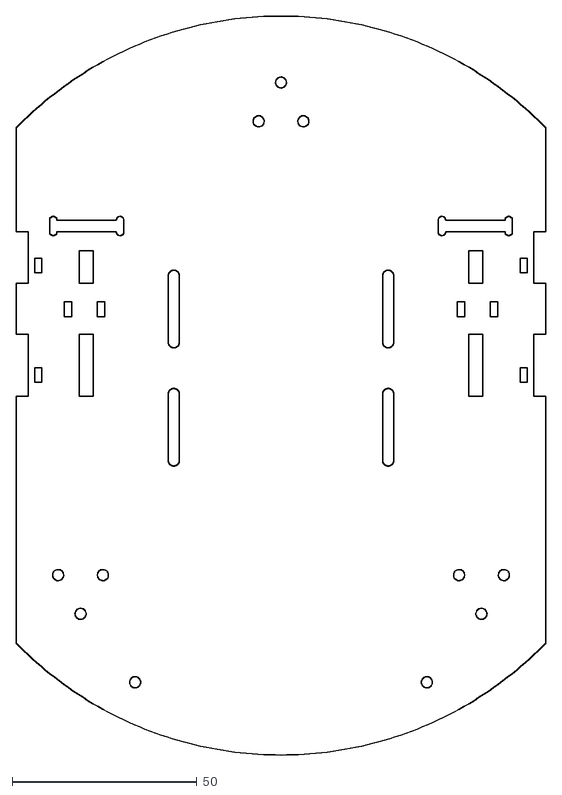
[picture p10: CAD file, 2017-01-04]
sawr_hardware/Parts/simple_base.dxf
143.4 x 200.0

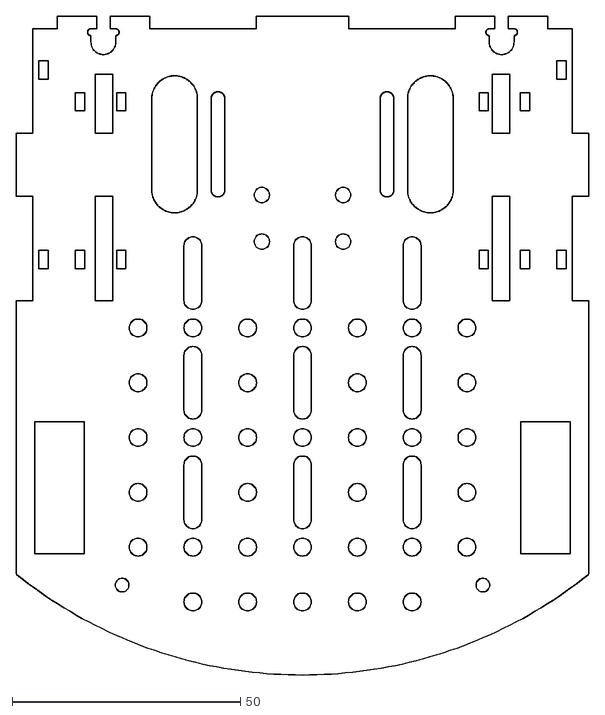
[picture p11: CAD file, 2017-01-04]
sawr_hardware/Parts/top_accessory.dxf
125.5 x 144.3

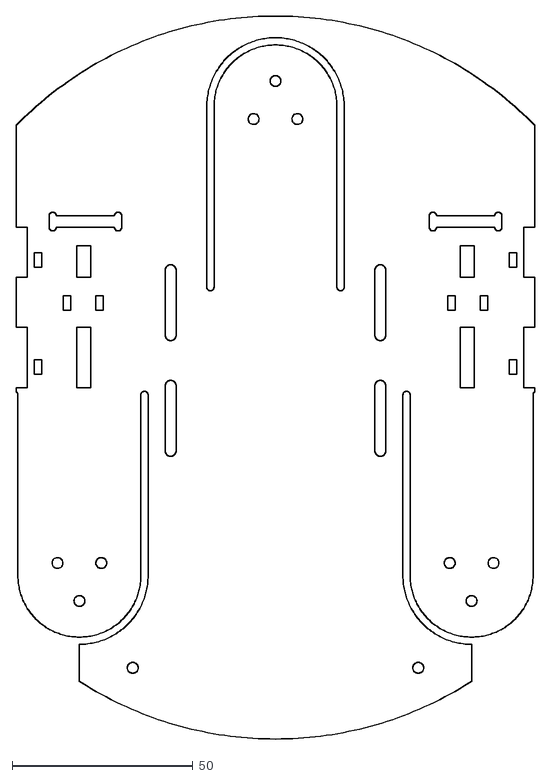
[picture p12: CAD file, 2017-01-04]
sawr_hardware/Parts/base.dxf
143.4 x 200.0

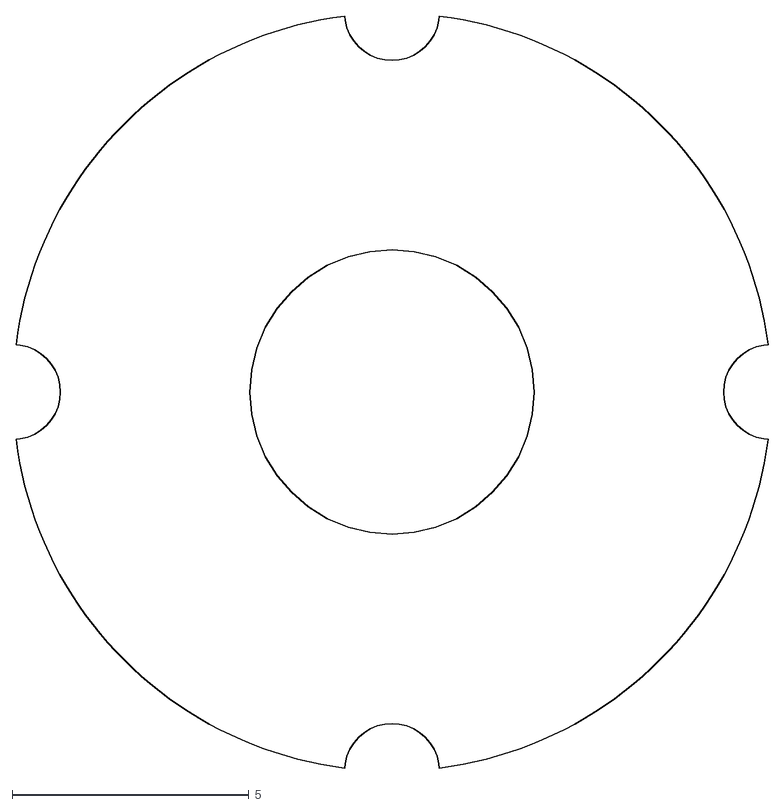
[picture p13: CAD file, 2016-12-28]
sawr_hardware/Parts/driver_spacer.dxf
15.9 x 15.9

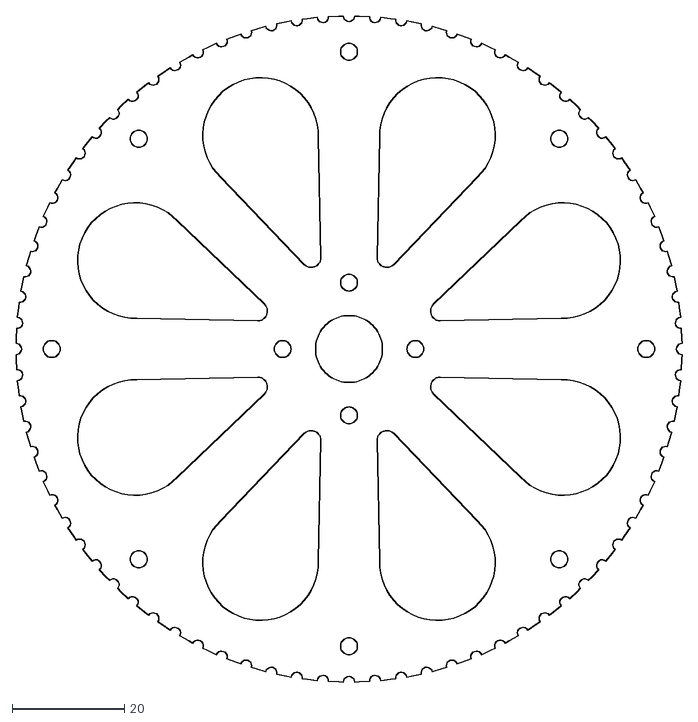
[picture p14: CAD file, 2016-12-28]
sawr_hardware/Parts/inner_wheel.dxf
118.4 x 118.4

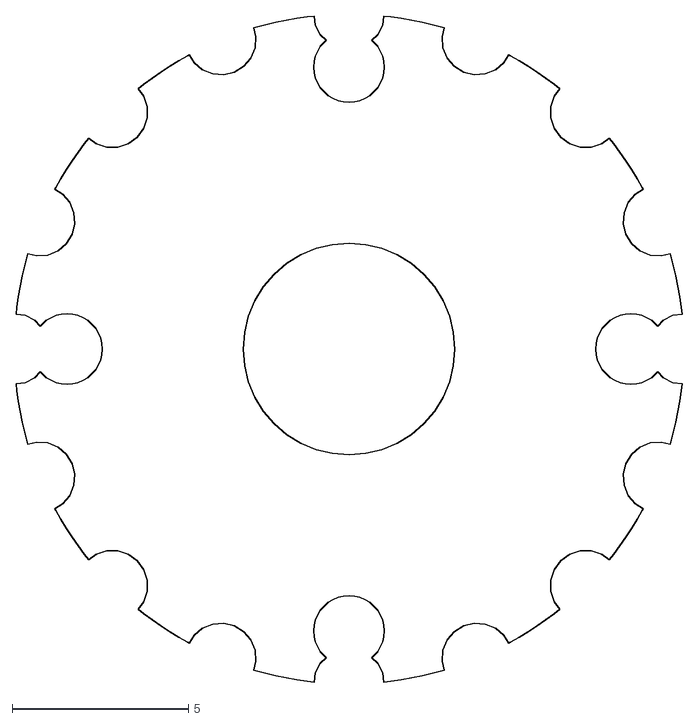
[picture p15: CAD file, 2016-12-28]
sawr_hardware/Parts/driver.dxf
18.9 x 18.9

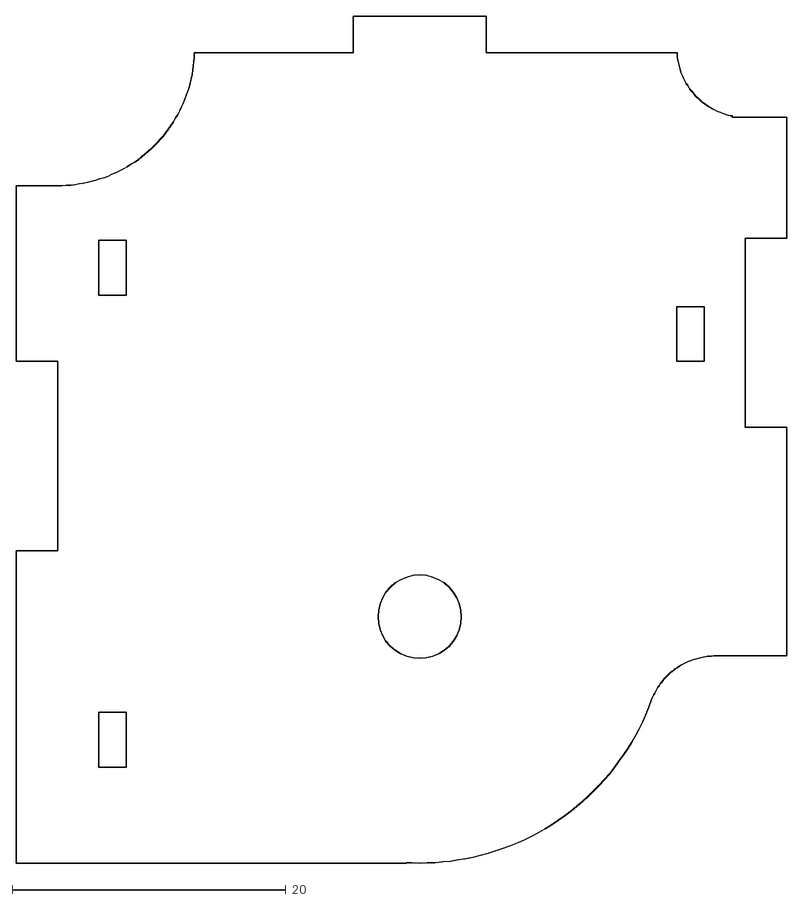
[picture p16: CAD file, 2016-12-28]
sawr_hardware/Parts/inner_mount.dxf
56.3 x 61.9

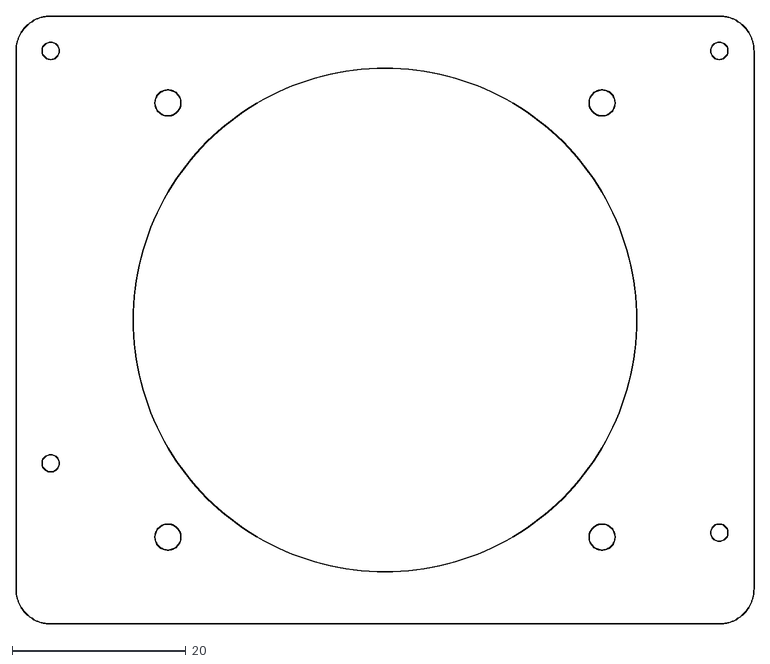
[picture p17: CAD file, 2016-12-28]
sawr_hardware/Parts/fan_plate.dxf
85.0 x 70.0

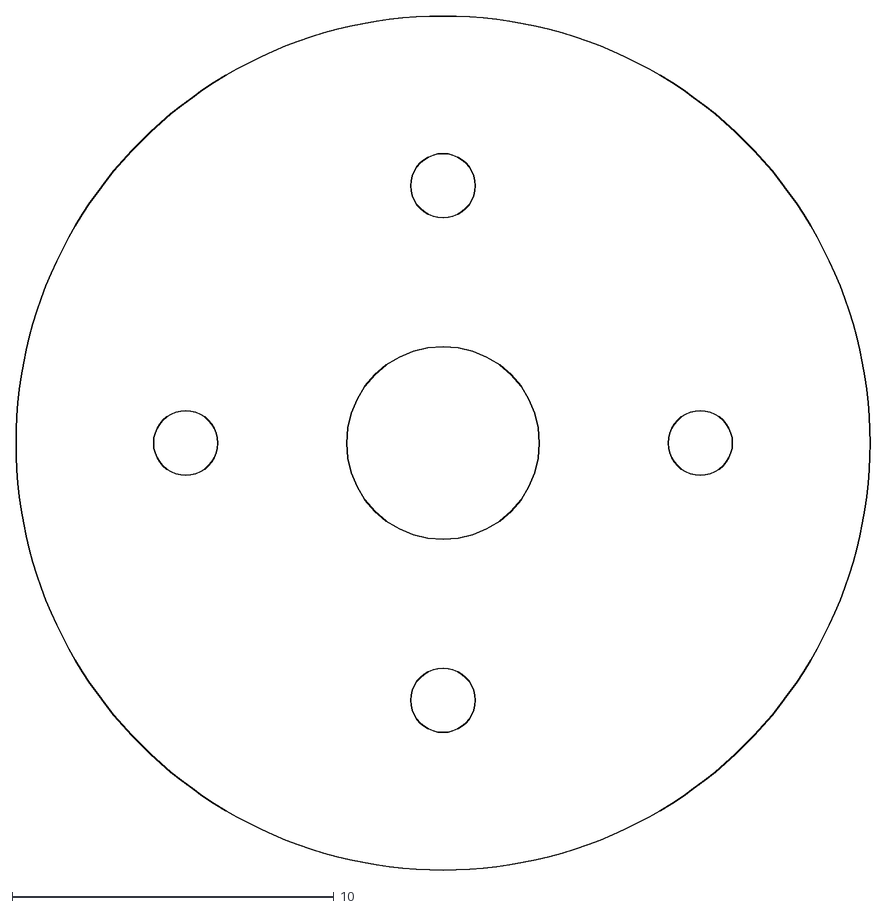
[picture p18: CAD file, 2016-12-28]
sawr_hardware/Parts/driver_rim.dxf
26.6 x 26.6

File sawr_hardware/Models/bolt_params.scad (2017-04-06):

// Nuts, Bolts, Spacers, Standoffs, Washers, etc.
//  For visualization only.  
//  Models are missing important details (like threads).
// Developed by: Michael McCool
// Copyright 2017 Intel Corporation
// License: CC-BY-4.0.  See LICENSE.md

// normally include the following externally, so comment out here
//include <tols.scad>
//include <smooth.scad>

// convenience function
function hex_size_to_radius(size) = size / (2 * cos(30));

// Smoothness

// Default colors
bolt_color = [0.5,0.5,0.7,0.9];
nut_color = [0.5,0.6,0.6,0.9];
spacer_color = [0.5,0.5,0.5,0.9];

// Radius of *unthreaded* part of the shaft (exact only for shoulder)
m2_shaft_radius   = 2/2;
m2_5_shaft_radius = 2.5/2;
m3_shaft_radius   = 3/2;
m4_shaft_radius   = 4/2;
m5_shaft_radius   = 5/2;
m6_shaft_radius   = 6/2;

// Threaded part of the shaft is slightly narrower
m2_thread_radius   = 1.86/2;
m2_5_thread_radius = 2.36/2;
m3_thread_radius   = 2.86/2;
m4_thread_radius   = 3.82/2;
m5_thread_radius   = 4.82/2;
m6_thread_radius   = 5.82/2;

// Cap radius
m2_cap_radius   = 4/2;
m2_5_cap_radius = 4.7/2;
m3_cap_radius   = 5.7/2;
m4_cap_radius   = 7.22/2;
m5_cap_radius   = 8.72/2;
m6_cap_radius   = 10.22/2;

// Cap height
m2_cap_height   = 2*m2_shaft_radius;
m2_5_cap_height = 2*m2_5_shaft_radius;
m3_cap_height   = 2*m3_shaft_radius;
m4_cap_height   = 2*m4_shaft_radius;
m5_cap_height   = 2*m5_shaft_radius;
m6_cap_height   = 2*m6_shaft_radius;

// Socket size (from hex face to hex face)
m2_socket_size   = 1.58;
m2_5_socket_size = 2.08;
m3_socket_size   = 2.58;
m4_socket_size   = 3.08;
m5_socket_size   = 4.1;
m6_socket_size   = 5.14;

// Socket radius (center to hex vertex)
m2_socket_radius   = hex_size_to_radius(m2_socket_size);
m2_5_socket_radius = hex_size_to_radius(m2_5_socket_size);
m3_socket_radius   = hex_size_to_radius(m3_socket_size);
m4_socket_radius   = hex_size_to_radius(m4_socket_size);
m5_socket_radius   = hex_size_to_radius(m5_socket_size);
m6_socket_radius   = hex_size_to_radius(m6_socket_size);

// Nut size (from hex face to hex face)
m2_nut_size   = 4;
m2_5_nut_size = 5;
m3_nut_size   = 5.5;
m4_nut_size   = 7;
m5_nut_size   = 8;
m6_nut_size   = 10;

// Nut radius (from center to hex vertex)
m2_nut_radius   = hex_size_to_radius(m2_nut_size);
m2_5_nut_radius = hex_size_to_radius(m2_5_nut_size);
m3_nut_radius   = hex_size_to_radius(m3_nut_size);
m4_nut_radius   = hex_size_to_radius(m4_nut_size);
m5_nut_radius   = hex_size_to_radius(m5_nut_size);
m6_nut_radius   = hex_size_to_radius(m6_nut_size);

// Nut height (face height for lock nuts)
m2_nut_height   = 1.6;
m2_5_nut_height = 2;
m3_nut_height   = 2.4;
m4_nut_height   = 3.2;
m5_nut_height   = 4;
m6_nut_height   = 5;

// Locknut height
m2_locknut_height   = 2.5;
m2_5_locknut_height = 3.8;
m3_locknut_height   = 4;
m4_locknut_height   = 5;
m5_locknut_height   = 5;
m6_locknut_height   = 6;

// Radius to use when cutting a hole for a given bolt size
m2_hole_radius   = m2_shaft_radius + tol/2 + cut_t;
m2_5_hole_radius = m2_5_shaft_radius + tol/2 + cut_t;
m3_hole_radius   = m3_shaft_radius + tol/2 + cut_t;
m4_hole_radius   = m4_shaft_radius + tol/2 + cut_t;
m5_hole_radius   = m5_shaft_radius + tol/2 + cut_t;
m6_hole_radius   = m6_shaft_radius + tol/2 + cut_t;

// "Standard bolt" defaults - for M3 x 10
bolt_shaft_length     = 10;
bolt_shouldere_length = 0;
bolt_shaft_radius     = m3_shaft_radius;
bolt_thread_radius    = m3_thread_radius;
bolt_shaft_sm         = 2*sm_base;
bolt_cap_radius       = m3_cap_radius;
bolt_cap_height       = m3_cap_height;
bolt_socket_size      = m3_socket_size;
bolt_socket_radius    = m3_socket_radius;

bolt_cap_sm           = 4*sm_base;
bolt_shoulder_sm      = 4*sm_base;
bolt_thread_sm        = 2*sm_base;
bolt_hole_sm          = 2*sm_base;

// "Standard nut" defaults - for M3
nut_height = m3_nut_height;
nut_size   = m3_nut_size;
nut_radius = m3_nut_radius;

// "Standard locknut" defaults - for M3
locknut_face_height = m3_nut_height;
locknut_height      = m3_locknut_height;
locknut_size        = m3_nut_size;
locknut_radius      = m3_nut_radius;

// Spacers
m2_spacer_height       = 6;
m2_spacer_hole_radius  = m2_shaft_radius + 2*tol;
m2_spacer_outer_radius = m2_nut_radius;
m2_5_spacer_height       = 6;
m2_5_spacer_hole_radius  = m2_5_shaft_radius + 2*tol;
m2_5_spacer_outer_radius = m2_5_nut_radius;
m3_spacer_height       = 6;
m3_spacer_hole_radius  = m3_shaft_radius + 2*tol;
m3_spacer_outer_radius = m3_nut_radius;
m4_spacer_height       = 6;
m4_spacer_hole_radius  = m4_shaft_radius + 2*tol;
m4_spacer_outer_radius = m4_nut_radius;
m5_spacer_height       = 6;
m5_spacer_hole_radius  = m5_shaft_radius + 2*tol;
m5_spacer_outer_radius = m5_nut_radius;
m6_spacer_height       = 6;
m6_spacer_hole_radius  = m6_shaft_radius + 2*tol;
m6_spacer_outer_radius = m6_nut_radius;

// Spacer defaults
spacer_height       = 6;
spacer_hole_radius  = m3_hole_radius + tol;
spacer_hole_sm      = 2*sm_base;
spacer_outer_radius = spacer_hole_radius + 2;
spacer_outer_sm     = 4*sm_base; 

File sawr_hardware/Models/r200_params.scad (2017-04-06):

// Basic Model of Intel(R) RealSense(TM) R200 Depth Camera
//   also includes cutting plan for basic mounting
// Developed by: Michael McCool
// Copyright 2017 Intel Corporation
// License: CC-BY-4.0.  See LICENSE.md

// All units in mm unless noted otherwise.

// CAMERA PARAMETERS

// basic overall size of camera
r200_x = 129;
r200_y = 8.2;
r200_z = 19.4;

// size and location of slot in camera
r200_sx = 60;
r200_sz = 4;
r200_six = 1.4;
r200_siz = 1.4;

// CAMERA MOUNT PARAMETERS
// size of mounting slot in frame
r200_mount_slot_x = 4; // width of slot
r200_mount_slot_y = 2; // height of slot
r200_mount_slot_ey = 1; // slot notch depth (behind camera)
r200_mount_slot_ix = 5; // offset of notch from end of camera

r200_mount_hole_r = m3_hole_radius;
r200_mount_hole_ix = r200_six + r200_mount_hole_r;
r200_mount_hole_iz = r200_siz + r200_sz/2;
r200_mount_hole_dx = r200_sx - r200_mount_hole_r - r200_six;
r200_mount_hole_sm = 4*sm_base;

// thickness of magnetic mounting plate and tape
r200_plate_thick = 1.4;

// defaults 
r200_mount_hole_p = 0.5;  // relative location of inner mounting hole
r200_mount_hole_t = 0.2;  // tolerance of mounting hole
r200_mount_slot_t = 0.0;  // tolerance of mounting slot

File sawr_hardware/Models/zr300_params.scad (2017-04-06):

// Parameters for Intel(R) RealSense(TM) ZR300 Depth Camera
// Developed by: Michael McCool
// Copyright 2017 Intel Corporation
// License: CC-BY-4.0.  See LICENSE.md

// CAMERA PARAMETERS

// basic overall size of camera
zr300_x = 156;
zr300_y = 9.5;
zr300_z = 32.5;

// base of camera
zr300_base_x1 = 32;
zr300_base_x2 = 57;
zr300_base_z = 3;
zr300_base_h = 18; // separation of mounting holes
zr300_base_r = m2_5_hole_radius;

// thickness of magnetic mounting plate and tape
zr300_plate_thick = 1.4;

// CAMERA MOUNT PARAMETERS

// size of mounting slot in frame
zr300_mount_slot_x = 4; // width of slot
zr300_mount_slot_y = 2; // height of slot
zr300_mount_slot_ey = 1; // slot notch depth (behind camera)
zr300_mount_slot_ix = 5; // offset of notch from end of camera

// defaults 
zr300_mount_hole_t = 0.2;  // tolerance of mounting hole
zr300_mount_slot_t = 0.0;  // tolerance of mounting slot

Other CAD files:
sawr_hardware/Parts/mount.dxf
sawr_hardware/Parts/rim_wheel.dxf
sawr_hardware/Parts/driver_mount.dxf
sawr_description/hardware/frame.scad
sawr_hardware/Models/bolts.scad
sawr_hardware/Models/frame.scad
sawr_hardware/Models/r200.scad
sawr_hardware/Models/smooth.scad
sawr_hardware/Models/smooth_make.scad
sawr_hardware/Models/smooth_model.scad
sawr_hardware/Models/tols.scad
sawr_hardware/Models/zr300.scad
sawr_hardware/Parts/inner.dxf
sawr_hardware/Parts/middle_wheel.dxf

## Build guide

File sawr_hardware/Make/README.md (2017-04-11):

Simple Autonomous Wheeled Robot (SAWR)
======================================
Making a Frame
--------------
Frame, driver and wheel components are laser cut from two Acrylic or POM sheets: 
one 2mm thick and the second 3mm thick.

Acrylic is perfectly fine and is low-cost, but POM (also known as Acetal, 
Delrin, or Duracon) is more durable and is recommended for heavy use, such as
in a classroom, or if you need to transport the robot frequently. Using Acrylic
only for the 2mm sheet but POM for the 3mm sheet is also possible and gives
most of the benefit of using POM alone.

If you just want to laser-cut the file, start with the PDF file, being careful
not to resize it. If you do not have access to the size of sheet specified in
the PDF file, you can rearrange the parts using a 2D vector graphics editor 
such as [Inkscape](https://inkscape.org/), which is free. In this case, you 
want to start from the SVG file. If you need to rearrange the file with Adobe 
Illustrator, however, start from the PDF file, as Adobe Illustrator tends to
resize SVG on import. 

The lines in these files have been colored red and blue. Red lines should be 
cut first, followed by the blue lines (i.e. Trotec conventions). Basically,
the outline of a part needs to be cut last so it is only freed from the main
sheet once all interior features have been cut. Depending on your laser cutter
(i.e. if you have a Universal laser cutter), you may have to modify the colors
to get the right cutting order. Depending on the laser cutter model the cut
time is between 24 min to 1 hr.  

### Sheet 1: 2mm Thick
You can access the cut files locally.  Use the appropriate format for your
laser cutter.  PDF is generally recommended unless you need to do editing.
Use one of the following to cut parts from a 2mm sheet of either Acrylic or POM:
* [Laser Cut file for 2mm sheet in SVG format](2mm.svg)
* [Laser Cut file for 2mm sheet in PDF format](2mm.pdf)

### Sheet 2: 3mm Thick
If you are using Acrylic, use one of these files to cut a 3mm sheet:
* [Laser Cut file for 3mm sheet in SVG format for Acrylic](3mm_acrylic.svg)
* [Laser Cut file for 3mm sheet in PDF format for Acrylic](3mm_acrylic.pdf)

If you are using POM and want a cantilevered suspension, use one of the 
following files instead for the 3mm sheet:
* [Laser Cut file for 3mm sheet in SVG format for POM](3mm_pom.svg)
* [Laser Cut file for 3mm sheet in PDF format for POM](3mm_pom.pdf)

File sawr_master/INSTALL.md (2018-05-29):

Simple Autonomous Wheeled Robot (SAWR)
======================================
Software Installation
---------------------
Follow these instructions to set up the software stack on your robot.
Once set up, refer to [LAUNCH.md](LAUNCH.md) for instructions on how to
run and use the software stack.

SAWR uses ROS (Robot Operating System, an open-source middleware framework for
robotics) but this is _not_ a tutorial on how to use ROS for mobile autonomous
robotics.  Please see the [ROS wiki](http://wiki.ros.org/) and also the many
excellent [books on ROS](http://wiki.ros.org/Books). Please also visit and
follow the [SAWR 01.org project page](https://01.org/sawr) for more
discussion, information, and resources for learning about robotics
using SAWR.

Install Ubuntu 16.04
--------------------
The SAWR software stack is based on [ROS Kinetic][ROS] which currently works
best under "desktop" [Ubuntu 16.04][Ubuntu]. Both the [Intel&reg; Joule&trade;][Joule]
and the [UP Board from Aaeon][UP] support desktop versions of Ubuntu 16.04.

**SECURITY NOTE:** During setup, it is highly recommended that you _DO NOT_ use
a username or password that are used elsewhere, and also you _DO NOT_ store
personal information (including web browser caches or web service account
credentials) on the robot. You may also want to use a separate account for
administration and run the SAWR software on an account on the robot on without
sudo access. As noted later, among other issues, remote access to ROS can be insecure
unless you take special effort to secure it.

### UP Board (included with the Intel Realsense Robotic Development Kit)
Follow instructions at
[https://up-community.org/wiki/Ubuntu](https://up-community.org/wiki/Ubuntu)
to first set up a standard distribution of Ubuntu 16.04 on your UP Board.

In summary, first
[download an ISO image for Ubuntu 16.04](https://www.ubuntu.com/download/desktop)
and load it onto a bootable USB stick using, for instance,
[Rufus](https://www.ubuntu.com/download/desktop/create-a-usb-stick-on-windows) 
or [Win32DiskImager](https://wiki.ubuntu.com/Win32DiskImager) under Windows,
or, if you have Ubuntu running already on another computer, the
[Startup Disk Creator](https://www.ubuntu.com/download/desktop/create-a-usb-stick-on-ubuntu).

**NOTE:** for performance reasons it is preferrable to install a lightweight variant
such as Xubuntu or Lubuntu. However, the normal Unity-based Ubuntu distribution
works fine and generally is more consistent with existing documentation, so try
that first... you can always reconfigure the window manager later if you want.
Ubuntu Core and Ubuntu Server have _not_ been tested with this release.

Then boot the UP Board and tap the DEL key to get into the BIOS (if it prompts
for a password just press enter). Go to the Boot menu and make the
first boot option be the USB drive, then press F4 to save and boot.

If you can be online during the boot process things will go smoother.
The simplest way to do this is to use a wired connection, since you
might have to install drivers for your WiFi dongle in a later step.

After you have installed Ubuntu, install the special kernel for the UP board,
using basically the following sequence (see the page on the
[UP Board wiki](https://wiki.up-community.org/Ubuntu) for the latest instructions
on installing Ubuntu).

    sudo add-apt-repository ppa:ubilinux/up
    sudo apt update
    sudo apt-get autoremove --purge 'linux-.*generic'
    sudo apt-get install linux-image-generic-hwe-16.04-upboard
    sudo reboot
 
As of this writing the instructions for modifying GRUB to boot the UP kernel
by default are missing a few things. In particular, to get the system to bring
up the GRUB menu on boot and to "save" the last kernel booted, you need to 
ensure the following two lines are in `/etc/default/grub` (using `sudoedit`).
Add the second line if necessary.

    GRUB_DEFAULT=saved
    GRUB_SAVEDEFAULT=true

You should also ensure that the following line is commented out as shown:

    # GRUB_HIDDEN_TIMEOUT=0

After making these changes to `/etc/default/grub`, run

    sudo update-grub

After selecting the `*-upboard` kernel manually at least once during boot
using the "Advanced" options, reboot _without_ selecting a kernel manually
and confirm that what `uname -r` produces still has `upboard` in the name.

This special UP kernel, in addition to providing access to board features
like GPIOs, already includes the RealSense uvc patches, saving us a step later.

### Intel Joule 
There is a special install of Ubuntu 16.04 for Joule available from
[Canonical](https://developer.ubuntu.com/core/get-started/intel-joule#alternative-install:-ubuntu-desktop-16.04-lts).

**NOTE:** for ROS, currently you want to install "Desktop Ubuntu" rather than 
"Ubuntu Core". You probably also need to update the Joule BIOS to the latest
version first as indicated. Updating the BIOS is relatively straightforward
but you will need a Windows computer with USB-3.0 and the USB3.0-to-USB-C 
cable included in the Joule development kit.

This version of Ubuntu also provides access to GPIOs, etc. The Realsense 
drivers are also already included in the kernel, so we can skip the uvc patch
later.

Currently only standard desktop Ubuntu (running Unity) is supported, not
Xubuntu or Lubuntu. However, if you really want XFCE or another lightweight 
window manager, it is possible to install it later and have it run by default 
(or even no window manager, which may make even more sense...).  

However, it is recommended to first complete a working install before trying
these options.

Open a Terminal Window
----------------------
You will need command line access to do most things. Click on the topmost icon
in the left menu bar with the Ubuntu logo, type "Terminal" in the search field,
then drag the terminal icon to the menu bar for later use.

Click it and open a terminal. To open additional terminals you need to right
click and select "New Terminal".

Install Basic Development Tools
-------------------------------
Enter the following to install git and basic development tools:

    sudo apt-get install git build-essential

Install WiFi Drivers (UP Board Only)
------------------------------------
Since the UP Board does not include WiFi, if you want wireless access you will
need to find a WiFi dongle and get it working. This will probably also involve
finding and installing drivers.  A 5GHz (ac) WiFi dongle is highly desireable
in this context but tends to only be supported by newer dongles that may not
yet have support built into the Linux distribution.

The TP-LINK AC600 (Archer T2UH) is a reasonable choice, as it supports both
2.4GHz and 5GHz bands and has a high-gain antenna. Driver installation for
this dongle looks like the following.

Note that (wired) network access is necessary as part of the process.

    mkdir -p ~/Drivers/T2UH
    cd ~/Drivers/T2UH
    git clone https://github.com/Myria-de/mt7610u_wifi_sta_v3002_dpo_20130916.git
    cd mt7610u_wifi_sta_v3002_dpo_20130916
    make
    sudo make install
    sudo cp RT2870STA.dat /etc/Wireless/RT2870STA/RT2870STA.dat

Then unplug your wired network and reboot. WiFi should come up automatically.
Log into your access point and test.

Add User to dialout Group
-------------------------
Membership in the `dialout` group is necessary to access the UART device for 
the [USB2AX](http://www.xevelabs.com/doku.php?id=product:usb2ax:quickstart)
which is used in turn to control the motors.

Add the current user to the ``dialout`` group as follows:

    sudo usermod -a -G dialout $USER

Then log out and log back in again. Check group membership using and confirm
`dialout` is listed:

    groups

Install Dynamixel SDK
---------------------
The [DynamixelSDK](https://github.com/ROBOTIS-GIT/DynamixelSDK) library
supports communication with the MX-12W "smart motors" used in the SAWR.

In theory you _should_ be able to install the Dynamixel SDK by installing the
`ros-kinetic-dynamixel` package, which is done below. In practice you need
the `dxl_monitor` program (see below) to configure your servos,
and currently that is unfortunately only available with a manual installation.

Here is a summary of how to install the Dynamixel SDK manually.  Note that
we also check out the `kinetic-devel` branch.  You need this if you want to
use `dxl_monitor` (see later section) as it depends on some functions in the
Dynamixel driver that have been deprecated in the latest versions.  More generally,
since we are using ROS Kinetic, we want a compatible version.

    mkdir -p ~/Drivers
    cd ~/Drivers
    git clone https://github.com/ROBOTIS-GIT/DynamixelSDK.git
    cd DynamixelSDK
    git checkout kinetic-devel
    cd c++/build/linux64
    make
    sudo make install

You will also have to configure the left servo with ID 1 (which in practice
means you leave it alone, since that is the default) and the right servo with
ID 2.

You can use the
[Dynamixel Wizard](http://support.robotis.com/en/software/roboplus/dynamixel_monitor.htm)
(yes, it does work with the USB2AX) from Windows to reconfigure the ID,
although it is also possible to do it directly from Linux.

To configure the servo IDs in Linux, go to your Dynamixel SDK install,
go to the `examples` directory, and compile the `dxl_monitor` program:

    cd ~/Drivers/DynamixelSDK/c++/example/dxl_monitor/linux64
    make
    
Then connect _just the **right** servo_ to the USB2AX.  Make sure it still has power,
however, since the USB2AX does not provide it.  This will require temporarily
reorganizing the servo cabling to disconnect and bypass the left servo.
The problem is that
by default all servos have the ID of 1, so having both on the bus at once will
lead to a conflict.  In order to change the ID of the right servo to a different
value we have to first make sure it is the only one on the bus.

In the above directory start the `dxl_monitor` program and do the following
(note that input is intermixed with output here):
```
./dxl_monitor --device /dev/ttyACM0

***********************************************************************
*                            DXL Monitor                              *
***********************************************************************

Succeeded to open the port!

 - Device Name : /dev/ttyACM0
 - Baudrate    : 1000000

[CMD] scan
 [ID:001] Model No : 00360                ... SUCCESS 
..........................................................................................................................................................................................................................................................

Scan Dynamixel Using Protocol 2.0
............................................................................................................................................................................................................................................................

[CMD] w1 1 3 2

 Success to write

[CMD] scan

Scan Dynamixel Using Protocol 1.0
.
 [ID:002] Model No : 00360                ... SUCCESS 
..........................................................................................................................................................................................................................................................

Scan Dynamixel Using Protocol 2.0
............................................................................................................................................................................................................................................................

[CMD] exit
```
Basically what the `w1 1 3 2` command does here is write, using
Dynamixel Protocol 1, on the servo with ID 1, the value 2 to register 3.
Each MX-12W servo has a
[set of registers](http://support.robotis.com/en/product/actuator/dynamixel/mx_series/mx-12w.htm).
Register 3 corresponds to the ID, so this changes its ID to 2.
When you rescan, you see the (only) servo now has a new ID of 002.

Now you can put the servo wiring back to normal, as the default ID of 1 is fine for the other servo.
If you want you can rescan to make sure both servos are visible.

Use `help` with `dxl_monitor` if you run into trouble.   The `reset1` command is
also useful as it resets the servo to its factory settings.

We use the factory default baud rate of 1,000,000 in our motor driver so there is no
need to change that.

Install librealsense
--------------------
The [librealsense SDK](https://github.com/IntelRealSense/librealsense)
library supports the Intel RealSense cameras. The SAWR can use either the R200
or the ZR300 but the R200 is recommended for use with the UP Board and the 
ZR300 for use with the Joule.

(You should be able to install librealsense using the ros-kinetic-librealsense
package, which is done below.  You can skip this step and return to it for
a manual install if that does not work.)

Here is a summary of how to install librealsense manually.

    sudo apt-get install libusb-1.0-0-dev pkg-config libglfw3-dev cmake
    mkdir -p ~/Drivers
    cd ~/Drivers
    git clone https://github.com/IntelRealSense/librealsense.git
    cd librealsense
  
If you are using the R200 or ZR300, you have to use the "legacy" library (tagged as v1.12.1)
as version 2 no longer supports these (now obsolete...) cameras:
    
    git fetch --all --tags --prune
    git checkout tags/v1.12.1 -b legacy

Install the librealsense user-space SDK libraries as follows:

    mkdir build
    cd build
    cmake ../ -DBUILD_EXAMPLES=true
    make
    sudo make install

Make sure the camera is not plugged in, then run

    cd ..
    sudo cp config/99-realsense-libusb.rules /etc/udev/rules.d/
    sudo udevadm control --reload-rules && udevadm trigger

Plug in your camera, and check that it is recognized with

    sudo dmesg | tail -n 50

Make sure `/usr/local/lib` (the install location of `librealsense`) is on your
`LD_LIBRARY_PATH`; if necessary, add it explicitly in your `.bashrc`:

    echo "export LD_LIBRARY_PATH=$LD_LIBRARY_PATH:/usr/local/lib" >> ~/.bashrc

Finally, run a test such as

    cpp-capture

Which should display the color, depth, and IR channels from the camera.
If you are running headless, you can also use

    cpp-headless
    
which dumps

Install ROS Kinetic
-------------------
Follow the [online install instructions for ROS Kinetic](http://wiki.ros.org/kinetic/Installation/Ubuntu)
including sourcing the ROS setup script in your `.bashrc`.

A summary follows:

    sudo sh -c 'echo "deb http://packages.ros.org/ros/ubuntu $(lsb_release -sc) main" > /etc/apt/sources.list.d/ros-latest.list'
    sudo apt-key adv --keyserver hkp://ha.pool.sks-keyservers.net:80 --recv-key 421C365BD9FF1F717815A3895523BAEEB01FA116
    sudo apt-get update
    sudo apt-get install ros-kinetic-desktop-full
    sudo rosdep init
    rosdep update
    echo "source /opt/ros/kinetic/setup.bash" >> ~/.bashrc
    source ~/.bashrc
    sudo apt-get install python-rosinstall

Note this downloads about 500MB of data and can take an hour or more,
depending on your network connection.

Set Up a Catkin Workspace 
-------------------------
Follow [the Catkin workspace tutorial](http://wiki.ros.org/ROS/Tutorials/InstallingandConfiguringROSEnvironment)
to configure a Catkin workspace, a summary of which follows:

    mkdir -p ~/catkin_ws/src
    cd ~/catkin_ws/src
    catkin_init_workspace
    cd ~/catkin_ws/
    catkin_make

Add this workspace to your `.bashrc` as well:

    echo "source ~/catkin_ws/devel/setup.bash" >> ~/.bashrc
    source ~/.bashrc

When you start a new shell from now on your environment will have been set up
automatically.

Install SAWR Packages
---------------------
If you have not done it already, the SAWR software itself can be copied from
the [SAWR github repository](https://github.com/01org/sawr) as follows:

    cd ~/catkin_ws/src
    git clone https://github.com/01org/sawr.git

Install Extra ROS Dependencies
------------------------------
The SAWR package depends on a few other ROS packages.
If necessary these can be installed with ``apt-get`` as follows:

    sudo apt-get install ros-kinetic-dynamixel-sdk \
                         ros-kinetic-librealsense \
                         ros-kinetic-realsense-camera \
                         ros-kinetic-depthimage-to-laserscan \
                         ros-kinetic-gmapping \
                         ros-kinetic-move-base \
                         ros-kinetic-navigation \
                         ros-kinetic-teleop-twist-keyboard 

This _should_ also automatically pull in the RealSense and Dynamixel
drivers, but if not, you can try the manual installations above.

Compile SAWR Package
--------------------
Prepare code in the SAWR package for execution:

    cd ~/catkin_ws
    catkin_make

Remote Access and Security
--------------------------
No system is ever perfectly secure, and there are tradeoffs between 
functionality and security.
Ubuntu is [fairly secure by default](https://insights.ubuntu.com/2016/12/08/ubuntu-16-04-lts-security-a-comprehensive-overview/)
but there are various ways to [improve it](https://www.thefanclub.co.za/how-to/how-secure-ubuntu-1604-lts-server-part-1-basics).
However, if you want to support remote access to your robot to teleoperate
it or to remotely visualize ROS data you will have to do some work.
The following are suggestions, not a complete solution for secure access.

### SSH
SSH provides secure remote access to a Linux system, and allows you to log
into your robot without having to hook up a display, keyboard and mouse.
This is obviously useful when the robot is roaming around.

However, by default an SSH server is not installed on Ubuntu. You can 
however easily install it using:

    sudo apt-get install openssh-server
    
Follow the [instructions here][SSH] to configure it.

Note that for enhanced security, after installation you should set up
a public key, copy it to the computer you intend to access the robot with,
then disable all remote logins via password.

It is recommended to leave your passphrase blank (it complicates automated
logins) but use a 4096-bit RSA key and use ufw to limit the rate of
login attempts to compensate.

### Firewall
You should also [set up a firewall][UFW]. With the firewall enabled, if you want 
remote ssh access, then you need to explictly allow it:

    sudo ufw enable
    sudo ufw allow ssh

Although, as noted above, to improve security you might want to limit the
rate of login attempts:

    sudo ufw limit ssh
    
Once this is setup, you will be able to remotely and securely log into your
robot to start the SW stack and use keyboard teleop. If you use `ssh -X` 
you will even be able to open windows.

Unfortunately remote graphics such as in `rviz` does not work (there is 
support in OpenGL for remote graphics, but...) and using ROS remotely may
require disabling the firewall.

Depending on what you want to do, you may also want to allow the ntp and http
protocols:

    sudo ufw allow ntp
    sudo ufw allow http

### Secure Tunnelled VNC
You can also 
[set up a VNC and tunnel it over SSH](https://www.linode.com/docs/applications/remote-desktop/install-vnc-on-ubuntu-16-04) to provide a remote desktop graphical user interface.
If set up properly this can be reasonably secure and will allow graphical
applications like `rviz`, and although it will not be as performant as a wired
HDMI connection, of course.

The simplest way to set up VNC (and the way you will find most instructions describing
if you search for how to do this on the Web) is just to enable 
[Desktop Sharing](http://ubuntuhandbook.org/index.php/2016/07/remote-access-ubuntu-16-04/) in Ubuntu
then use the [Remmina remote desktop client](https://github.com/FreeRDP/Remmina/wiki/Remmina-User's-guide). 

However, Desktop Sharing has various issues. The most important limitation 
for our purposes is that Ubuntu's Desktop Sharing 
and Remmina use `tightvnc` which does not support 3D graphics,
so applications like `rviz` will not work. Therefore we recommend
using [TurboVNC](http://www.turbovnc.org/) which not only enables 3D graphics,
it also has significantly higher performance and quality than `tightvnc`.

Full setup instructions are given in [VNC.md](VNC.md).

### Remote ROS Access
Note that if the firewall is running then 
[remote network access to ROS](http://wiki.ros.org/ROS/NetworkSetup)
will not be possible. You can temporarily disable the firewall in this case 
using 

    sudo ufw disable

and of course reenable it with

    sudo ufw enable  
    
Unfortunately, while the firewall is disabled your robot will be vulnerable
and should not connected directly to a public network.

ROS is not defined with security in mind and should not be opened to an 
outside network. Unfortunately ssh tunneling will not work for remote ROS
access as ROS uses a number of dynamically allocated ports.

### OpenVPN
A more secure option for remote ROS access, and recommended if you want to 
access your robot remotely over the internet, is to set up a VPN.

Assuming your router/WiFi access point does not support running a VPN
in hardware, you probably will have to do this in software using something
like [OpenVPN][OpenVPN]. This is complex to set up but can give you secure
remote access to ROS.

### ROSbridge: Future Work
We are currently investigating rosbridge and how to secure a remote web 
console with Robot Web Tools.  However, note that the standard configuration
of rosbridge opens a port that allows anyone to access it using an insecure
websocket, so it's just as insecure as plain ROS.

However, ROSbridge also does support _secure_ websockets, and so with the
right setup, it should be possible to build a reasonably secure web API using
it.

We are investigating this. However, for the time being if you use a default
rosbridge configuration it is also recommended to do so only on a secure and
isolated network.

Next Steps
----------
The installation should now be ready to launch.
See [LAUNCH.md](LAUNCH.md) for further instructions.

[ROS]: http://wiki.ros.org/kinetic
[Ubuntu]: http://releases.ubuntu.com/16.04/
[Joule]: https://software.intel.com/en-us/iot/hardware/joule
[UP]: http://www.up-board.org/up/
[SSH]: https://help.ubuntu.com/community/SSH/OpenSSH/Configuring
[UFW]: https://www.digitalocean.com/community/tutorials/how-to-set-up-a-firewall-with-ufw-on-ubuntu-16-04
[OpenVPN]: https://www.digitalocean.com/community/tutorials/how-to-set-up-an-openvpn-server-on-ubuntu-16-04

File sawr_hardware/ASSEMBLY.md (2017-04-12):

Simple Autonomous Wheeled Robot (SAWR)
======================================
Assembly Instructions
---------------------

The SAWR is a simple learning platform for autonomous robotics. Despite its
small size and low cost, it is capable of performing advanced mobile robotics
tasks, including simultaneous localization, mapping, and navigation.

The purpose of the SAWR is to provide a starting point for people who would
like to learn more about advanced mobile robotics, in particular autonomous
navigation and ROS, the Robot Operating System.

This simple robot (and its software stack) can also serve as a starting point
for those seeking to develop more sophisticated robots based on the
Intel&reg; RealSense&trade; Robotic Development Kit (RDK).

All frame components for the SAWR are parametrically designed with
[OpenSCAD](http://www.openscad.org/) and can be easily adjusted to accommodate
geometry of new electronic components if required. In addition to the 
Intel&reg; RealSense&trade; RDK, the frame also already has mounting points
for the Intel&reg; Joule&trade; development kit and the more advanced
Intel&reg; RealSense&trade; ZR300 3D camera.

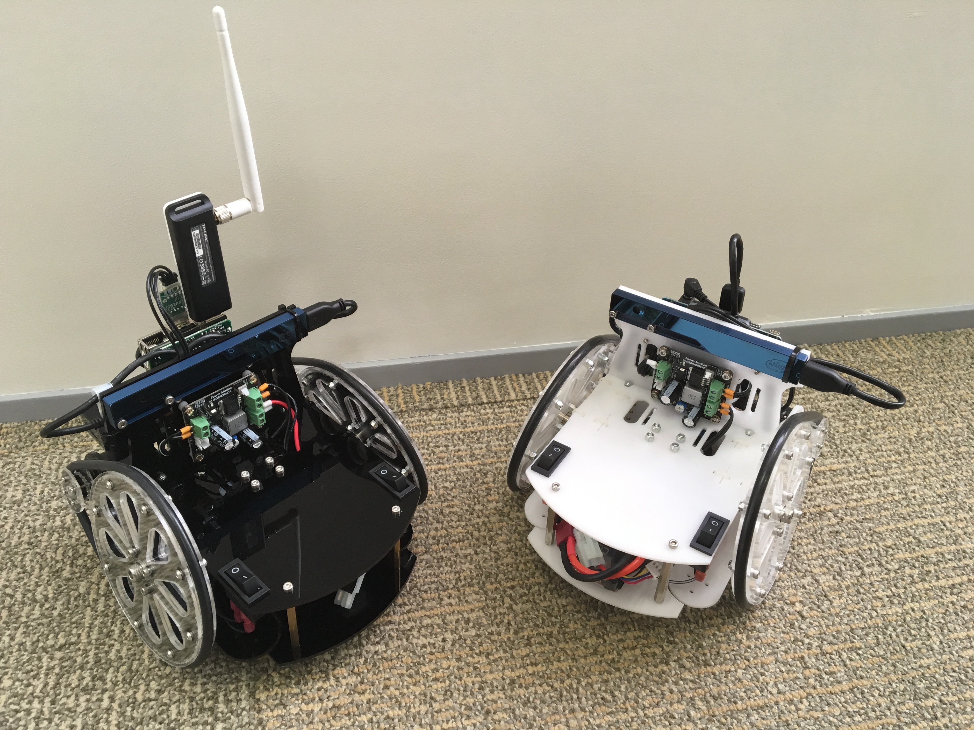
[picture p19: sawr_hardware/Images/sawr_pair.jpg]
SAWR Pair


The SAWR uses easily available off-the-shelf parts. This makes it possible to 
assemble a robot using locally-sourced and relatively inexpensive components.
The SAWR's locomotion is based on two Dynamixel MX-12W servos. While these are
a more "exotic" part these motors provide accurate odometry feedback and speed
control, and are well-supported by ROS and the robotics community. Since they
have internal MCUs the need for an external MCU and motor drivers is
eliminated, simplifying the overall design.

This document outlines all mechanical/electronic components and assembly steps
of the SAWR. Images have been included in the SAWR package to go with this 
file but links are also provided to additional files and even 3D models as
appropriate.

Mechanical Assembly and Electrical Wiring
-----------------------------------------

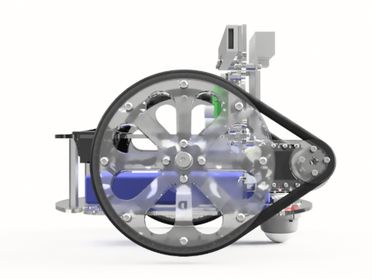
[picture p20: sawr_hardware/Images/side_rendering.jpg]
Side View - Rendering

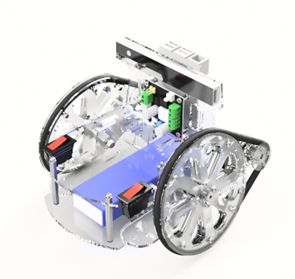
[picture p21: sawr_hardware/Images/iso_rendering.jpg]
Iso View - Rendering


All mechanical drawings, 3D assemblies, and electrical schematics presented
in this document are also available in the form of web links to CAD cloud
storage. In general, the online versions of these images and models may be 
more up-to-date than the images in this document, in addition to allowing
interaction, such as rotating a 3D model. Therefore, please follow the links
provided in any case where a clearer view is needed or to ensure you have the
latest version of the figure. You can also use OpenSCAD to look at the model
locally.

Fastener specifications and part numbers are provided in the [BOM](Materials) 
and 2D drawings.
Part numbers are from the [McMaster-Carr catalog](http://www.mcmaster.com/).
All fasteners are sized in metric. In many cases equivalent parts can be
substituted, so in addition to McMaster-Carr part numbers we also provide
(in BOM and drawings) generic specifications of each part so you can find
appropriate substitute parts if necessary.

Generally a 10% tolerance is assumed for the thickness of the plates making
up the frame and for the sizes of holes. For example, the slots for tabs on 
3mm plates are actually 3.3mm wide so plates that are a little thicker than
they are supposed to be will still work. The same is true for most bolt holes;
an M3 bolt hole is generally 3.2mm in diameter (the threaded part of an M3 bolt 
is actually slightly less than 3mm in diameter). This allows for both
manufacturing variance (eg for plates, which can very in thickness even within
a single sheet) and for the use of Imperial substitutions for bolts. One
exception however where an accurate size is needed is for the bearings and the
bolt used for the wheel axle. These must be exact as a press fit is used so 
either get metric bolts and bearings or edit the CAD files and/or PDF files
before cutting if you must make substitutions.

Cut sheets and instructions for making a frame are in the [Make](Make/README.md)
subdirectory.

Here is [a drawing](http://a360.co/2a88Qpd) of all laser cut components with 
the names we will be using to refer to them in the assembly notes.

The Tower plate provides the option to mount either the RDK kit (UP board and 
Intel RealSense R200) or an Intel Joule Development Kit with an Intel RealSense
ZR300 camera. It is also possible to combine a Joule with an R200 camera.

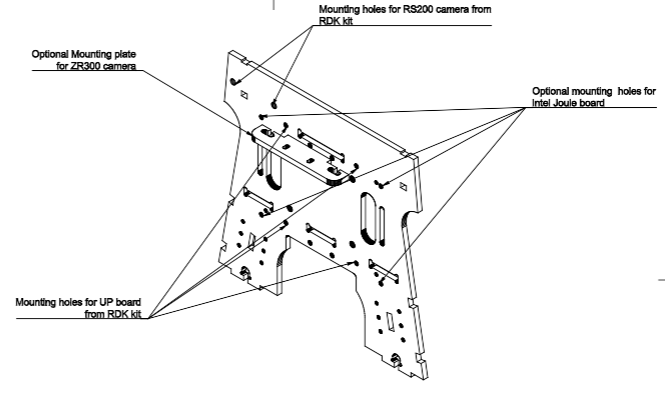
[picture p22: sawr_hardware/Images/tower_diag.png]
Tower Diagram


Here is a Bill of Materials (BOM), with estimated cost of parts. The links are for reference only; you may be able to find alternative suppliers for these parts.

Select Download from the following web pages:
* [Download BOM (Bill of Materials) in XLS format](http://a360.co/2c8y1bV)
* [Download BOM (Bill of Materials) in CSV format](http://a360.co/2c8xRBg)

A local version of the BOM is also available, but may be out of date:
* [Local BOM (Bill of Materials) in CSV format](Materials/BOM_RDK.csv)

Wheels Assembly
---------------

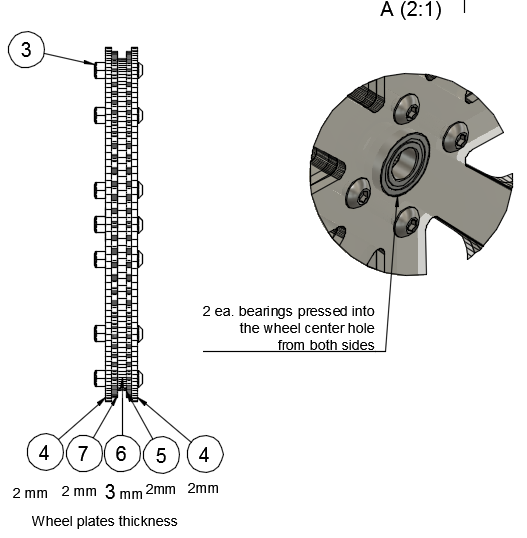
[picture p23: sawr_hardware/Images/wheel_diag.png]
Wheel Diagram


[_Drawing 1_](http://a360.co/29UsC8R)
([Wheel 3D Assembly](http://a360.co/2agnle2))

Wheels are assembled from five layers of laser cut components. This allows the
outer profile of the wheel to have a "U" shape to capture an O-ring tire, which
is also used as a belt drive. The center layer of each wheel is 3mm thick, and
all other layers are 2mm thick, providing 7mm clearance for the belt/tire
between the two outer layers of the wheel. The total wheel thickness is 11mm.

Assembly:

1. Press in two bearings into the center holes of two pairs of the outer 2mm
   wheel layers. This is easiest before bolting the wheel layers together as
   you can press in the bearing using a flat surface.

2. Secure all 5 layers of the wheel with 12 ea. M3 lock-nuts and M3x14 screws.
   The central layer's hole is slightly smaller than the outer diameter of the
   bearing, so the bearings will not pass through the center layer.

3. Repeat for the second wheel.

Frame Assembly
--------------

It is advisable to assemble the rest of the robot in the order given below.
Note the location of the holes on the top of the tower: the orientation of the
tower plate matters, it is not reversible!  The mounting holes for the 
single-board computers and the camera are not reversible.

Assembly:

1. Attach components to the Tower plate in the following order given by 
   Drawings 2A, 2B, and 2C below. 

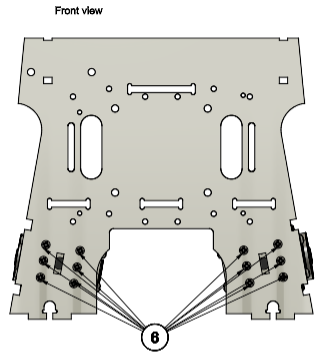
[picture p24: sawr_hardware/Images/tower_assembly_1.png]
Tower_Assembly 1
  
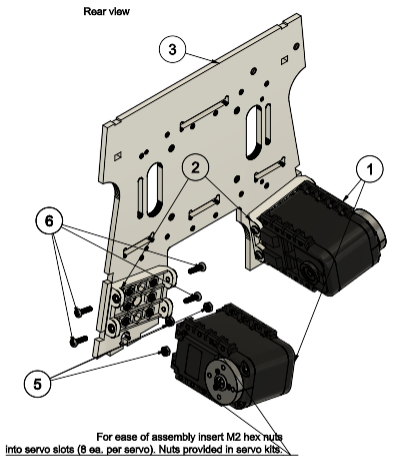
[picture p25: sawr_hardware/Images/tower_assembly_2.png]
Tower_Assembly 2
  
     
   [_Drawing 2A_](http://a360.co/2covpJj)
   ([Tower 3D Assembly](http://a360.co/2ago66G))
      
* Attach two brackets to the tower. For each bracket, install 6ea. M2 hex nuts
  (provided in individually packaged servo boxes) in the bracket and use 6ea. 
  M2x8 screws to secure bracket to the Tower. 

* Repeat for the second bracket.
  
* Insert M2 nuts into the servos, both along the outer faces (8 ea.) and along
  the end where the bracket goes (4 ea.). We will only be using the latter for
  now but it is much easier to install the nuts in the servos _before_ mounting
  them on the robot.

* Attach two servos to the brackets. For each servo, use 4 ea. M2x8 screws and
  4 ea. M2 hex nuts (M2 nuts are provided with individually packaged servos).

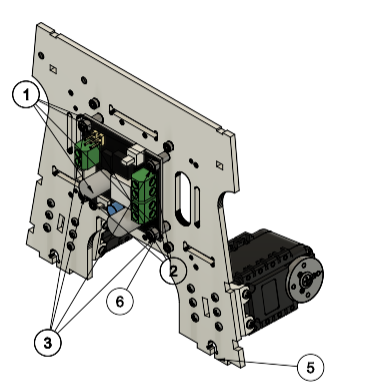
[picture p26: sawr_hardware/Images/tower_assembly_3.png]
Tower_Assembly 3
  
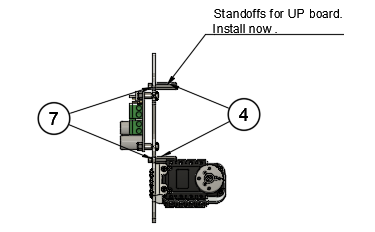
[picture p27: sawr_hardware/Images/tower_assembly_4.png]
Tower_Assembly 4
  
    
  [_Drawing 2B_](http://a360.co/2coACk9)

* Install the DFRobot DC-DC Power Convertor. The power convertor goes on the
  opposite side of the tower from the servos. Note the orientation of the
  connectors; when viewed from the side the power convertor is mounted on,
  the 5V output should be on the left. When viewed from the _back_, where the
  servos are, the 5V output will be on the right. Use 4ea. M3x6mm spacers, 
  4ea. M3 locknuts and 4 ea. M3x14 screws. 
  
* **Make sure the output voltage selection switch is in the 5V position.**

* Install standoffs for the UP board, but do not attach the UP board to the
  tower yet. We will install UP board after we organize the wiring, much of
  which will run underneath the UP board. Use 4ea M2.5x16 mm standoffs and
  4ea M2.5x6 screws. 

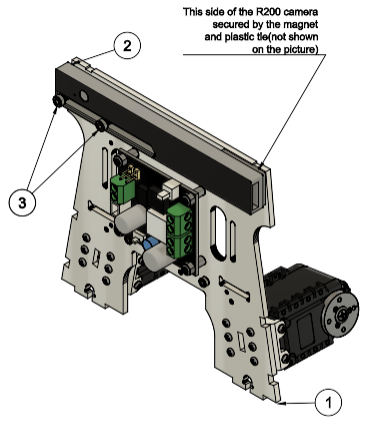
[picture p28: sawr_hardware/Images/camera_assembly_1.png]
Camera Assembly 1
  
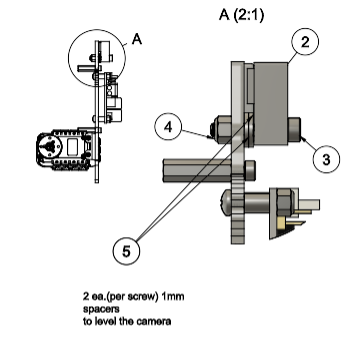
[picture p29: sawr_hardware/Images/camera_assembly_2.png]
Camera Assembly 2
  

  [_Drawing 2C_](http://a360.co/2afYBTa)

* Install the Intel&reg; RealSense&trade; R200 3D Camera. Use 2ea M3x18 socket
  head screws, 2 ea. M3 locknuts, 1 ea. sticky magnet (included in camera kit)
  and 1 ea. cable tie. Use 4ea. (2ea. per screw) M3x1mm washers as a spacers
  between camera and Tower. 
  
* The following procedure is recommended to install the camera to ensure
  precise horizontal and vertical alignment:

    * Insert 1ea. M3x18 screw into slot in camera.
    
    * Add 2 ea. M3x1mm washers to the screw between camera and Tower.
    
    * Loosely secure screw with M3 locknut in the outer camera mount hole in the tower.
    
    * The camera should still be able to rotate and slide freely.
    
    * Attach the magnet to the other side of the camera, making sure it is in 
      an accurate position.  The bump in the magnet should be in the slot on 
      the back of the camera.
      
     * Remove protective paper from the magnet but do not stick it to the tower.
    
     * Align camera vertically and horizontally: the top edge of the camera 
       should be exactly aligned with the top tower edge.
    
     * Press sticky side of the magnet to tower.
    
     * Secure the locknut.
    
     * Secure the second screw with washers and a locknut.
    
     * Do not overtighten either screw. The locknuts and screws should hold 
       the camera firmly without bending the case of the camera.

2. Top Plate

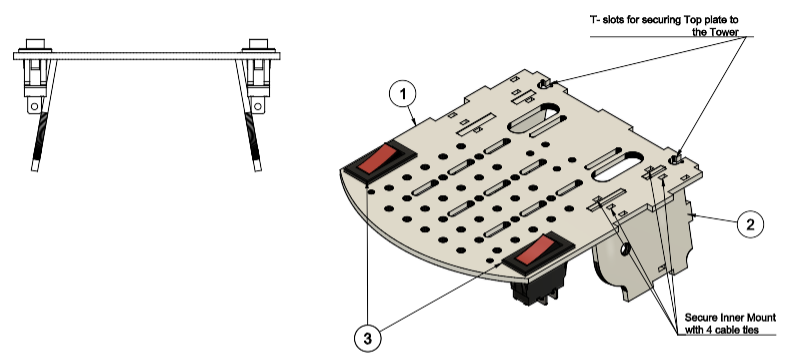
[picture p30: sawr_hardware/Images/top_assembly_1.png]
Top Assembly 1
  

  [_Drawing 3A_](http://a360.co/2a3N9qc) 
  ([3D Assembly](http://a360.co/2a3nbTS))

* Attach 2 ea. Inner Mount Plates to the Top Plate and secure with 2 ties. 
  Leave ties semi loose. Don't cut ties excess length yet. 
  
* Install 2 ea. Switches.

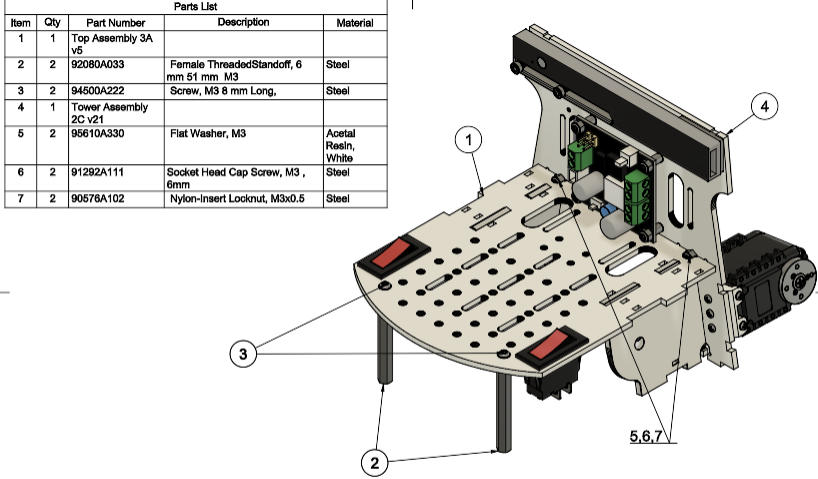
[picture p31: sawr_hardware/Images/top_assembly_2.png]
Top Assembly 2
  
  
  [_Drawing 3B_](http://a360.co/2a3n1Mc)

* Attach Top Plate to the Tower with 2 ea. M3x6 screws, M3 nuts, M3x1 washers
  in T-slots. 
  
    - NOTE: Using a little masking tape to hold the T-slot nuts in place during
      assembly can make this a lot easier.  
  
* Tighten ties and cut off excess tie length. 
  
* Install 2 ea. M3x51mm standoffs. Use 2ea. M3x8 button head screws.

* Secure Outer Mount Plate to the Servo with 8ea. M2x8 screws and 8ea. M2 hex
  nuts.  Repeat for the second Outer Mount.

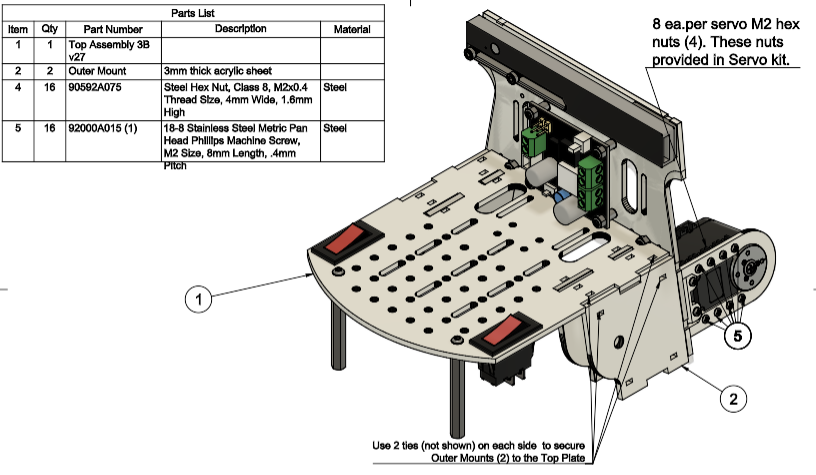
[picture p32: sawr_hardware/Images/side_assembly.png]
Side Assembly
  

  [_Drawing 3C_](http://a360.co/2a3orGD)
    
* Attach Outer Mount Plates to Top Plate with ties.

3. Install Axles and Wheels but do not secure the M5 axle nut tightly yet. 
   Repeat for the second Wheel.
     
     - NOTE: It is possible to substitute an M6 nut and bolt for the M5
       shoulder bolt used here, as long as at least 12mm of the shaft of 
       the bolt is unthreaded and the unthreaded part of the shaft is actually
       6mm in diameter. Shoulder bolts are generally machined more exactly 
       than unthreaded bolts.
  
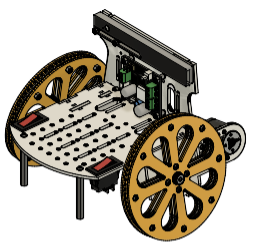
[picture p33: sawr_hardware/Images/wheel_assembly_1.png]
Wheel Assembly 1
  
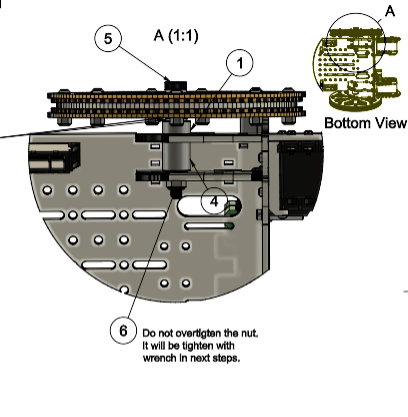
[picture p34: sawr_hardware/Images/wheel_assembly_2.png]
Wheel Assembly 2
  

  [_Drawing 4_](http://a360.co/2a3nPRi)
  ([3D Assembly](http://a360.co/2a3N1Y2))
  
* At this point you may want to do the wiring as described in the 
  Wiring section below. However, it is relatively easy to take off the base
  plate later if necessary.

4. Base Plate

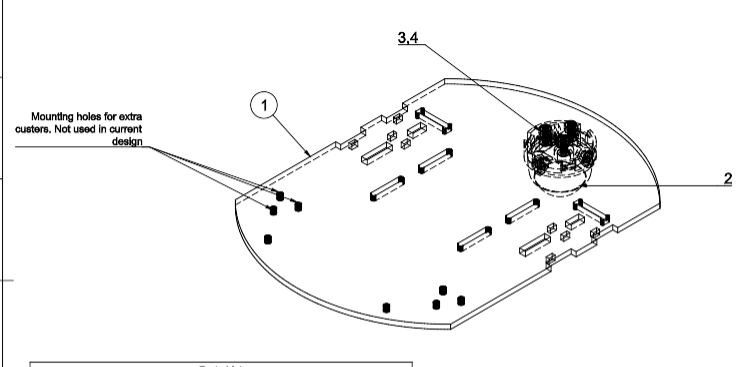
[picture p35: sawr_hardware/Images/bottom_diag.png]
Bottom Diagram
  

  [_Drawing 5A_](http://a360.co/2a3zOys)
  ([Base 3D Assembly](http://a360.co/2agoFxm))

  * Install the ball caster on the Base plate with 3ea. M3x8 screws and 3ea. 
    M3 locknuts. The basic design uses only one caster in the rear part of the
    robot, but you may add 2 more front casters if you want; this will reduce
    the ability of the robot to go over obstacles but will also make it less
    liable to tipping forward when decelerating. The extra mounting holes on
    the front of the Base Plate provide this option.  

      * Only the POM version of the base plate has flexible "suspensions" for 
        the casters.  If cut in Acrylic these have proven to break too easily 
	and so the basic version of the 3mm sheet omits them.
      * The frame is intentionally designed so that the casters do not all 
        touch the ground at the same time.

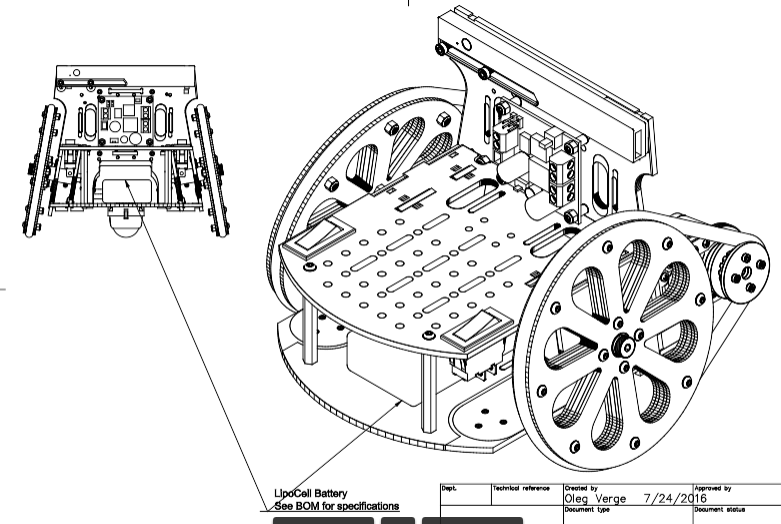
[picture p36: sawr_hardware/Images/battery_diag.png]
Battery Diagram
    

    [_Drawing 5B_](http://a360.co/2a88AGJ)

  * Insert Velcro straps in the slots of the Base Plate and install the 
    Battery. Overlap the straps underneath the robot so they can be loosened
    without taking off the Base Plate.
   
  * You should remove the battery after fitting it, then slide it back in 
    afterwards.  You might also want to fit the straps (and remove the battery 
    again) before fitting the Base Plate. 
  
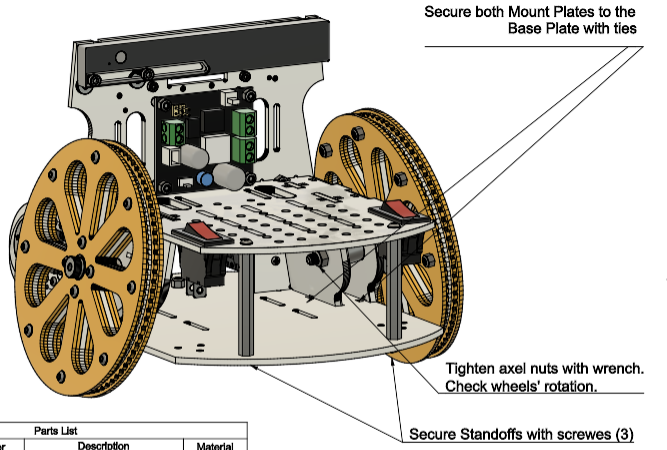
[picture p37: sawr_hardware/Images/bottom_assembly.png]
Bottom Assembly
    
  
    [_Drawing 5C_](http://a360.co/2a3zYpA)
  
  * Secure front Standoffs to the Base Plate with 2 ea. M3x8 screws

  * Attach Base Plate to the Tower and secure it with 2ea. M3x6 screws, 
    3ea. M3 nuts, and 3ea. M3x1mm washers in T-slots.

    - NOTE: Using a little masking tape to hold the T-slot nuts in place during
      assembly can make this a lot easier.  
     
  * Secure Outer and Inner Mount Plates to the Base Plate with ties 
    (on both sides).
  
  * Tighten Axle bolt with a wrench. Check that Wheels rotate freely on the 
    Axle.

      * **Do not overtighten.**  

      * Best practice is to tighten until you start to feel slight resistance,
        then back off a half turn.

5. Driver and O-rings. 

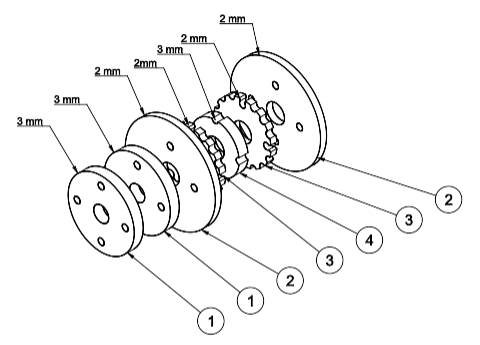
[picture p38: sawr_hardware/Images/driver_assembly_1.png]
Driver Assembly 1
  
  
  [_Drawing 6A_](http://a360.co/2a82vKJ)
  ([3D Assembly](http://a360.co/2akZt8Y))

  * Stack Driver components in your hand and align bolt holes.
    
  * Insert 4 ea. M2x20mm screws into stack, then secure driver onto the 
    servo hub.
  
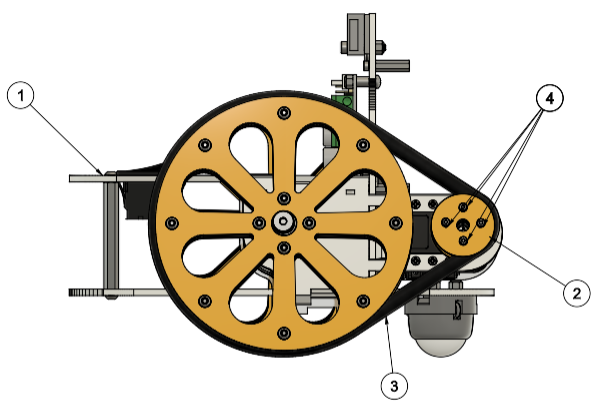
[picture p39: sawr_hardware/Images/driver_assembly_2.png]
Driver Assembly 2
   
  
  [_Drawing 6B_](http://a360.co/2akV7Pf) 

  * Install Driver and O-Ring by placing O-Ring over the Driver first
    and then stretching it around the grooves on the Wheel.

Wiring 
------
For ease of assembly you may want to complete wiring immediately after step 3 
of the mechanical assembly, eg before attaching the Base Plate. Otherwise,
you may want to remove the Base Plate temporarily.

6. Power

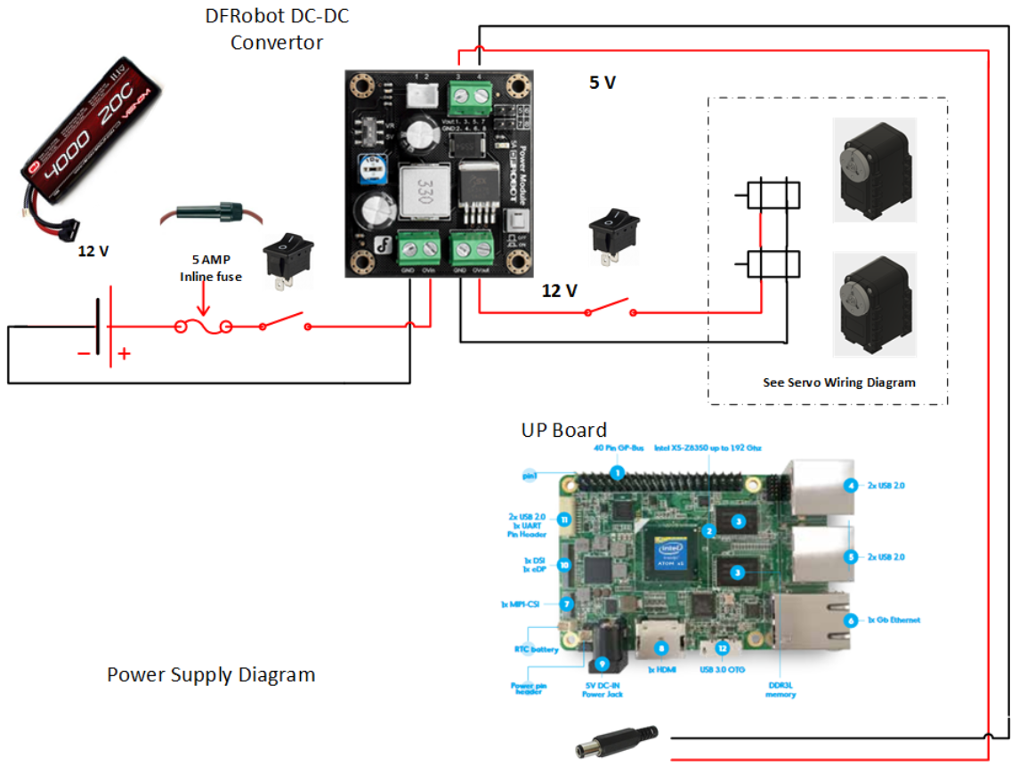
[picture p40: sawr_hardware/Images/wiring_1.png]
Wiring 1
  
    
  [_Drawing 7: Power Supply Wiring Diagram_](http://a360.co/2a8p4yC)
    
  * We have used the Venom 20C 3S 4000mAh 11.1V LiPo Battery with
    good results. In our tests this battery provides enough power for 
    about 60 min of active operation.
    
      - Get a
	[battery monitor](https://hobbyking.com/en_us/hobbykingtm-lipo-voltage-checker-2s-8s.html)
	to monitor the voltage of the battery and
        make sure never to discharge any cell below 3.4V.   In fact, you should
	avoid going below 3.6V (on any cell) to extend the life of your battery.
	  
      - Do not leave the battery monitor plugged in when the robot is in storage.
	Otherwise the monitor will slowly drain (and kill) your battery.
	  
      - Observe proper safety precautions with the battery.  In particular,
        do not charge the battery while it is in the robot: remove it and
        charge it in a fire-safe bag.  Follow the manufacturer's instructions
        on charge rate and do not overcharge.
	  
      - To extend the lifetime of the battery, best practice is to charge slowly,
        at a 0.5C rate (eg charge a 4000mAh battery at a rate of 2A),
        and not to a full charge each time, say to 12.4V rather than 12.6V.
	It is possible to charge faster, but it will reduce the life of your battery.
	
      - If you need to leave the robot in storage for a while, try to not do so 
        with the battery near a full charge.   Instead it should be between 75%
	and 80% full.
	  
      - **BE VERY CAREFUL NOT TO SHORT-CIRCUIT THE BATTERY TERMINALS.**  These 
        batteries can discharge at a very high rate, and short-circuiting the 
        battery will cause a fire hazard.
    
  * You may also want to consider creating a barrel connector to battery-plug
    adapter cable so you can power the system from an external power supply during
    software configuration.  However, please be aware of the following:
       
      - You want to connect the external supply _instead_ of the battery, **not**
        in parallel with it.
	 
      - You need a 12V external power supply of at least 5A.  A 3A supply is
        insufficient to power both the motors and the UP Board.
	 
      - **BE VERY CAREFUL NOT TO PLUG THIS ADAPTER DIRECTLY INTO YOUR UP BOARD.
        The UP Board requires a 5V regulated supply.  Plugging 12V into it 
        directly will destroy it.**

  * Main electrical power is distributed from the battery through an in-line 
    5 AMP fuse. The positive side is routed through the main power rocker 
    switch to the DC-DC convertor.  The DC-DC convertor provides 5V output
    but also provides a pass-through 12V connection. The pass-through 12V line
    is used to power the Servos using a modified Dynamixel cable while the 
    5V line is used to power the UP Board with a center-positive 5.1mm 
    barrel connector.

  * Pay special attention to the correct polarity of the wires when connecting
    to DC-DC convertor. If you get this wrong you can destroy your UP Board
    and/or your servos. 
    
      * It is **strongly** recommended to use a voltmeter to check both the 
        output voltage and the polarity before plugging in the servos or the 
	UP Board! 
	
      * See also the 
        [DFRobot Manufacturer Instructions](http://www.dfrobot.com/index.php?route=product/product&amp;product_id=752#.V5etZTU2eXg).

      * Double-check that the output voltage is set to 5V (small switch on the 
        DC-DC convertor).  Leaving this switch in the wrong position is another
	way to destroy your UP Board.

  * Also be careful when wiring up the power from the battery. We know of at 
    least one person that has completely destroyed a SAWR by wiring up their
    battery backwards.

7. Servo Wiring

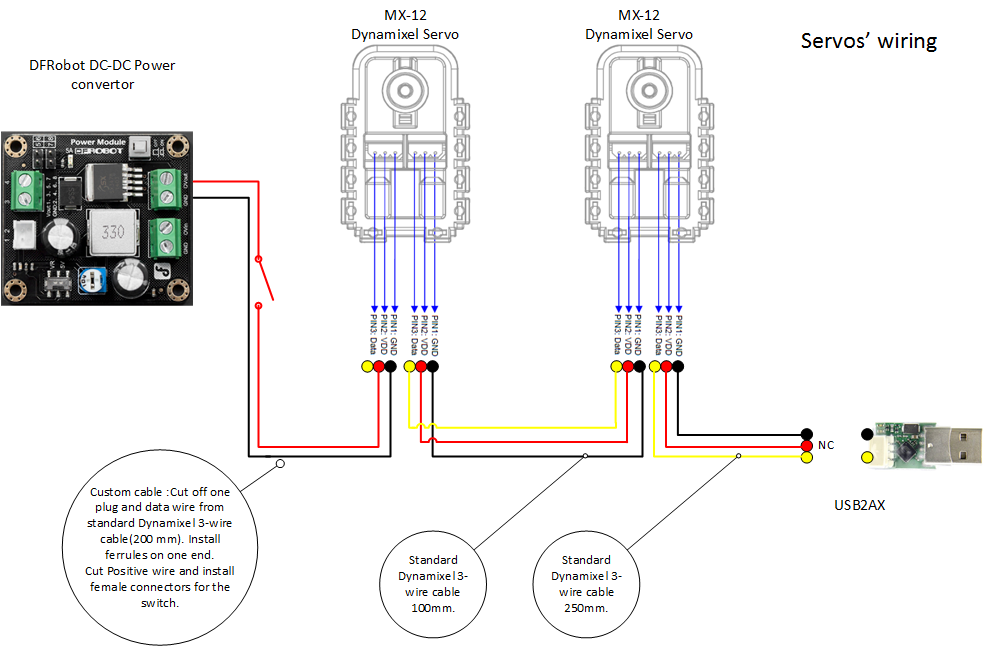
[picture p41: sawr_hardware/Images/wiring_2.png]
Wiring 2
   
   
  [_Drawing 8: Servo Wiring Diagram_](http://a360.co/2a8p5CN)
  
  * Connect USB2AX to 1st servo using a 250mm Dynamixel cable.
 
  * Interconnect both servos with Dynamixel 100mm cable.
  
  * Using a "custom" cable, connect the 2nd servo to the pass-through output
    power connector of the DC-DC power convertor.
  
      * This cable can be created by modifying a normal Dynamixel cable.
  
      * The "red" wire (the center wire of the Dynamixel cable) connects to 
        OVout on the pass-though screw terminal on the DC-DC convertor and the 
	"black" wire connects to GND on the same connector. 

          * See wiring diagram, and note especially the keying on the 
	    Dynamixel cables.
     
      * Unfortunately you will have to use the connector keying to distinguish
        the ground and the signal cables since they are not actually colored
	or labelled in any way!
 
      * The "red" wire of the custom cable has 2 female connectors that should
        be attached to the second rocker switch.
	
	  * This rocker switch will control power supply to motors only, which 
	    will allow you to turn off or reset the motors, but keep the UP 
	    Board powered. This is useful both to preserve battery life when
	    you need to work on UP Board configuration and programming, and
	    to stop the motors if necessary without crashing the UP Board.
  
8. USB Connections

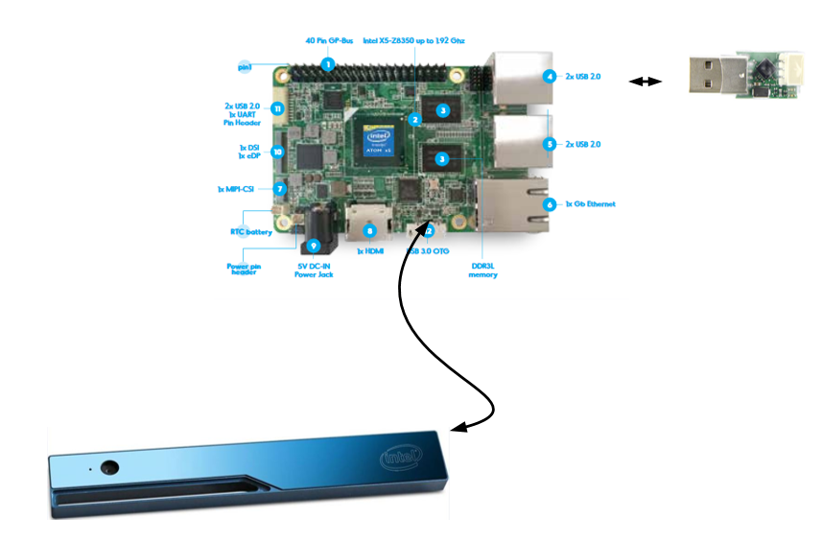
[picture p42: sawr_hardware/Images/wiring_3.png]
Wiring 3
   

  [_Drawing 9_: USB Connections](http://a360.co/2ajdTqA)
  ([USB Connection Diagram](http://a360.co/2ci6REp))

  * Connect the RealSense R200 Camera to the USB3 OTG port on the UP Board 
    with the short 3.0 micro-B to micro-B USB3.0 cable provided in the RDK.
     
  * Plug the USB2AX adapter into a (regular) USB2 port of the UP Board.

  * It is advisable to route camera and USB2AX cables in between the Tower 
    and UP Board. Address cable management and secure UP Board to the Tower 
    plate with 4ea. M2.5x6 screws. You may also want to capture the cables
    using cable management clips and/or cable ties.

     * Note that the USB3.0 plug on the UP Board is fragile and can be 
       broken off easily (guess how we know this...). Avoid putting vertical
       pressure on this cable. It is strongly advised to provide strain relief
       on the cable protruding from this port in particular.
     
  * Insert Wi-Fi USB dongle into UP board.

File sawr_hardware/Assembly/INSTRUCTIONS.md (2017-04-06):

# Simple Autonomous Wheeled Robot (SAWR) Assembly Instructions

The SAWR is a simple learning platform for autonomous robotics. Despite its small size and low cost, it is capable of performing advanced mobile robotics tasks, including simultaneous localization, mapping, and navigation. 

The purpose of the SAWR is to provide a starting point for people who would like to learn more about advanced mobile robotics, in particular autonomous navigation and ROS, the Robot Operating System.

This simple robot (and its software stack) can also serve as a starting point for those seeking to develop more sophisticated robots based on the Intel&reg; RealSense&trade; RDK.

All frame components for the SAWR are parametrically designed with [OpenSCAD](http://www.openscad.org/) and can be easily adjusted to 
accommodate geometry of new electronic components if required. In addition to the Intel&reg; RealSense&trade; RDK, the frame also already has mounting points for the Intel&reg; Joule&trade; development kit and the ZR300 Intel&reg; RealSense&trade; 3D camera.

The SAWR uses easily available off-the-shelf parts.  This makes it possible to assemble a robot using locally-sourced and inexpensive components. The SAWR's locomotion is based on two Dynamixel MX-12W servos.  While these are a more "exotic" part these motors provide accurate odometry feedback and speed control, and are well-supported by ROS and the robotics community.  Since they also have internal MCUs for speed control the need for an external MCU and motor drivers is eliminated, simplifying the overall design.

This document outlines all mechanical/electronic components and assembly steps of the SAWR. Images have been included in the SAWR package to go with this file but links are also provided to high-resolution files and even 3D models as appropriate.

## Mechanical Assembly and Electrical Wiring

Side View - Rendering
Iso View - Rendering

All mechanical drawings, 3D assemblies, and electrical schematics presented in this document are also available in the form of web
links to CAD cloud storage. In general, the online versions of these images and models may be more up-to-date than the images in this document, in addition to in many cases allowing interaction, such as rotating the 3D model. Therefore, please follow the links in any case where a clearer view is needed or to ensure you have the latest version of the figure. You can also use OpenSCAD to look at the model locally.

Fastener specifications and part numbers are provided in the BOM and 2D drawings. Part numbers are from the [McMaster-Carr catalog](http://www.mcmaster.com/).

All fasteners are sized in metric. In many cases equivalent parts can be substituted, so in addition to McMaster-Carr part numbers we also provide (in BOM and drawings) generic specifications of each part so you can find appropriate substitute parts if necessary.

Generally a 10% tolerance is provided for in holes and slots.  For example, the slots for tabs on 3mm plates are actually 3.3mm wide so plates that are a little thicker than they are supposed to be will still work.  The same is true for most bolt holes; an M3 bolt hole is generally 3.2mm in diameter (the threaded part of an M3 bolt is actually slightly less than 3mm in diameter).  This allows for both manufacturing variance (eg for plates) and the use of Imperial substitutions for bolts.  One exception however where an accurate size is needed is for the bearings and the bolt used for the wheel axle. These must be exact so either get metric bolts and bearings or edit the CAD files and/or PDF files before cutting if you must make substitutions.

Frame, driver and wheel components are laser cut from two 450mm x 300mm (18x12 in) Acrylic or Acetal sheets: one 2mm thick and the second 3mm thick. Acrylic is perfectly fine and is low-cost, but Acetal (also known as POM, Delrin, or Duracon) is more durable and is recommended for heavy use, such as in a classroom, or if you need to transport the robot frequently. Using Acrylic only for the 2mm sheet but Acetal for the 3mm sheet is also possible and gives most of the benefit of using Acetal alone.

If you just want to laser-cut the file, start with the PDF file, being careful not to resize it. If you do not have access to the size
of sheet specified, you can rearrange the parts using a 2D vector graphics editor such as [Inkscape](https://inkscape.org/), which is free. In this case, you want to start from the SVG file. If you need to rearrange the file with Adobe Illustrator, however, start from the PDF file, as Adobe Illustrator tends to resize SVG on import. In addition, the lines in these files have been colored red and blue.  Red lines should be cut first, followed by the blue lines (Trotec conventions). Basically, the outline of a part needs to be cut last so it is only freed from the main sheet once all interior features have been cut. Depending on your laser cutter (i.e. if you have a Universal laser cutter), you may have to modify the colors to get the right cutting order. Depending on the laser cutter model the cut time is between 24 min to 1 hr.

### Sheet 1:450X300x2 mm
(18x12x0.078 in) -- 1 each.

Select Download from the following web pages:
* [Download Laser Cut file for 2mm sheet in SVG format](http://a360.co/2aKxAYn)
* [Download Laser Cut file for 2mm sheet in PDF format](http://a360.co/2iRK3wz)

### Sheet 2:450x300x3mm
(18X12x0.118in) -- 1 each.

Select Download from the following web pages:
* [Download Laser Cut file for 3mm sheet in SVG format](http://a360.co/2iRDmuA)
* [Download Laser Cut file for 3mm sheet in PDF format](http://a360.co/2iRBB0e)

Here is [a drawing](http://a360.co/2a88Qpd) of all laser cut components with the names we will be using to refer to them in the assembly notes.

The Tower plate provides the option to mount either the RDK kit (UP board and Intel RealSense RS200) or an Intel Joule development kit with an Intel RealSense ZR300 camera. It is also possible to combine a Joule with an R200 camera.

Tower Diagram

Here is a Bill of Materials (BOM), with estimated cost of parts. The links are for reference only; you may be able to find alternative suppliers for these parts.

Select Download from the following web pages:
* [Download BOM (Bill of Materials) in XLS format](http://a360.co/2c8y1bV)
* [Download BOM (Bill of Materials) in CSV format](http://a360.co/2c8xRBg)

## Wheels Assembly

Wheel Diagram

[_Drawing 1_](http://a360.co/29UsC8R) ([Wheel 3D Assembly](http://a360.co/2agnle2))

Wheels are assembled from five layers of laser cut components. The outer profile of the wheel has a "U" shape to capture an O-ring tire, which is also used as a belt drive.  The center layer of each wheel is 3mm thick, and all other layers are 2mm thick. The total wheel thickness is 11mm.
* Press in two bearings into the center holes of two pairs of the outer 2mm wheel layers.
  This is easiest before bolting the wheel layers together as you can press in the bearing using a flat surface.
* Secure all 5 layers of the wheel with 12 ea. M3 lock-nuts and M3x14 screws.
  The central layer's hole is slightly smaller than the outer diameter of the bearing,
  so the bearings will not pass through the center layer.
* Repeat for the second wheel.

## Frame and assembly of other components

It is advisable to assemble the rest of the robot in the order given below. Note the location of the holes on the top of the tower: the orientation of the tower plate matters, it is not reversible!

1. Attach components to the Tower plate in the following order given by Drawings 2A, 2B, and 2C below. 

  Tower_Assembly 1
  Tower_Assembly 2
     
   [_Drawing 2A_](http://a360.co/2covpJj) ([Tower 3D Assembly](http://a360.co/2ago66G))
      
* Attach two brackets to the tower. For each bracket, install 6ea. M2 hex nuts (provided in servo box) in the bracket and use 6ea. M2x8 screws to secure bracket to the Tower. Repeat for the second bracket.
  
* Insert M2 nuts into the servos, both along the outer faces (8 ea.) and along the end where the bracket goes (4 ea.). We will only be using the latter for now but it is much easier to install the nuts in the servos _before_ mounting them on the robot.

* Attach two servos to the brackets. For each servo, use 4 ea. M2x8 screws and 4 ea. M2 hex nuts (nuts provided with servo kits).

  Tower_Assembly 3
  Tower_Assembly 4
    
  [_Drawing 2B_](http://a360.co/2coACk9)

* Install the DFRobot DC-DC Power Convertor.  The power convertor goes on the opposite side of the tower from the servos. Note the orientation of the connectors; when viewed from the side the power convertor is mounted on, the 5V output should be on the left. When viewed from the _back_, where the servos are, the 5V output will be on the right. Use 4ea. M3x6mm spacers, 4ea. M3 locknuts and 4 ea. M3x14 screws. Make sure the switch is in the 5V position.

* Install standoffs for the UP board, but do not install UP board yet. We will install UP board last after we organize the wiring, much of which will run underneath the UP board. Use 4ea M2.5x16 mm standoffs and 4ea M2.5x6 screws. 

  Camera Assembly 1
  Camera Assembly 2

  [_Drawing 2C_](http://a360.co/2afYBTa)

* Install the Intel&reg; RealSense&trade; RS200 3D Camera. Use 2ea M3x18 socket head screws, 2 ea. M3 locknuts, 1 ea. sticky magnet (included in camera kit) and 1 ea. cable tie. Use 4ea. (2ea. per screw) M3x1mm washers as a spacers between camera and Tower. 
  
* The following procedure is recommended to install the camera in order to ensure precise horizontal and vertical
     alignment:

    * Insert 1ea. M3x18 screw into slot in camera.
    
    * Add 2 ea. M3x1mm washers to the screw between camera and Tower.
    
    * Loosely secure screw with M3 locknut in the outer camera mount hole in the tower.
    
    * The camera should still be able to rotate and slide freely.
    
    * Attach the magnet to the other side of the camera, making sure it is in an accurate position (the bump in the magnet should be in the slot on the back of the camera) and remove protective paper from the magnet.
    
     * Align camera vertically and horizontally: the top edge of the camera should be aligned with the tower edge.
    
     * Attach sticky side of the magnet to tower.
    
     * Secure the locknut.
    
     * Secure the second screw with washers and a locknut
    
     * Do not overtighten either screw. The locknuts and screws should hold the camera firmly without bending the case of the camera.

2. Top Plate

Top Assembly 1

[_Drawing 3A_](http://a360.co/2a3N9qc) ([3D Assembly](http://a360.co/2a3nbTS))

* Attach 2 ea. Inner Mount Plates to the Top Plate and secure with 2 ties. Leave ties semi loose. Don't cut ties excess length yet. 
  
* Install 2 ea. Power On-Off switches.

  Top Assembly 2

  [_Drawing 3B_](http://a360.co/2a3n1Mc)

* Attach Top Plate to the Tower with 2 ea. M3x6 screws, M3 nuts, M3x1 washers in T-slots. Tighten ties and cut off excess tie length. 
  
* Install 2 ea. M3x51mm standoffs. Use 2ea. M3x8 button head screws.

* Secure Outer Mount Plate to the Servo with 8ea. M2x8 screws and 8ea. M2 hex nuts.  Repeat for the second Outer Mount.

  Side Assembly

  [_Drawing 3C_](http://a360.co/2a3orGD)
    
* Attach Outer Mount Plates to Top Plate with ties.

3. Install Axles and Wheels but do not secure the M5 axle nut tightly yet. Repeat for the second Wheel. NOTE: it is possible to substitute an M6 nut and bolt for the shoulder bolt used here, as long as at least 12mm of the shaft of the bolt is unthreaded and is actually 6mm in diameter.  Shoulder bolts are generally machined to be exact whereas unthreaded bolts are more approximate.
  
  Wheel Assembly 1
  Wheel Assembly 2

  [_Drawing 4_](http://a360.co/2a3nPRi) ([3D Assembly](http://a360.co/2a3N1Y2))
  
* At this point, for the ease of future assembly, you may want to address Servo wiring as described in the Servo Wiring section below.

4. Base Plate

  Bottom Diagram

  [_Drawing 5A_](http://a360.co/2a3zOys) ([Base 3D Assembly](http://a360.co/2agoFxm))

  * Install the ball caster on the Base plate with 3ea. M3x8 screws and 3ea. M3 locknuts. Current design uses only one caster in the rear part of the robot, but you may add 2 more front casters if you want; this will reduce the ability of the robot to go over obstacles but will also make it less liable to tipping forward when decelerating. The extra mounting holes on the front of the Base Plate provide this option.

  * Only the Acetal version of the base plate has flexible "suspensions" for the casters.  If cut in Acrylic these have proven to break too easily.  The frame is intentionally designed so that the casters do not all touch the ground at the same time in any case.

    Battery Diagram

    [_Drawing 5B_](http://a360.co/2a88AGJ)

  * Insert Velcro straps in the slots of the Base Plate and Install the Battery. 
   
  * You should remove the battery after fitting it, then slide it back in afterwards.  You might also want to fit the straps (and remove the battery again) before fitting the bottom plate. 
  
    Bottom Assembly
  
    [_Drawing 5C_](http://a360.co/2a3zYpA)
  
  * Secure front Standoffs to the Base Plate with 2 ea. M3x8 screws

  * Attach Base Plate to the Tower and secure it with 2ea. M3x6 screws, 3ea. M3 nuts, and 3ea. M3x1mm washers in T-slots.
     
  * Secure Outer and Inner Mount Plates to the Base Plate with ties (on both sides).
  
  * Tighten Axel bolt with a wrench. Do not overtighten. Check that Wheels rotate freely on the Axel.

5. Driver and O-rings. 

  Driver Assembly 1
  
  [_Drawing 6A_](http://a360.co/2a82vKJ) ([3D Assembly](http://a360.co/2akZt8Y))

  * Stack Driver components in your hand and align bolt holes.
    
  * Insert 4 ea. M2x20mm screws into stack, then secure driver onto the servo hub.
  
  Driver Assembly 2 
  
  [_Drawing 6B_](http://a360.co/2akV7Pf) 

  * Install Driver and O-Ring by placing O-Ring over the Driver first and then stretching it around the grooves on the Wheel.

## Wiring Components

6. Power

  Wiring 1
    
  [_Drawing 7: Power Supply Wiring Diagram_](http://a360.co/2a8p4yC)
    
  * In this design we are using Venom 20C 3S 4000mAh 11.1V LiPo Battery with Universal Plug.
    In our tests this battery provides enough power for 60 min of active operation.

  * Main electrical power is distributed from the battery through an in-line 5 AMP fuse.
    The positive side is routed through the main power rocker switch to the DC-DC convertor,
    where it splits into 5V and 12V supply lines. The 12V line is used to power the Servos
    using a modified Dynamixel cable while the 5V line is used to power UP board with a barrel connector.

  * Pay special attention to the correct polarity of the wires when connecting to DC-DC convertor.
    If you get this wrong you can destroy your UP Board and/or your servos. It is **strongly** recommended
    to use a voltmeter to check both the output voltage and the polarity before plugging in the servos or
    the UP Board!  See also the
    [DFRobot Manufacturer Instructions](http://www.dfrobot.com/index.php?route=product/product&amp;product_id=752#.V5etZTU2eXg).
    Double-check that the output voltage is set to 5V.

  * Also be careful when wiring up the power from the battery. We know of at least one person that has
    completely destroyed a robot by diligently wiring up their battery backwards.

7. Servo Wiring
  For ease of assembly you may want to complete this step immediately after step 3 of the mechanical assembly.

  Wiring 2 
   
  [_Drawing 8: Servo Wiring Diagram_](http://a360.co/2a8p5CN)
  
  * Connect USB2AX to 1st servo using a 250mm Dynamixel cable.
 
  * Interconnect both servos with Dynamixel 100mm cable.
  
  * Using "custom" cable, connect the 2nd servo to the pass-through output power connector of the DC-DC power convertor.
  
      * This cable can be created by modifying a normal Dynamixel cable.
  
      * The "red" wire (the center wire of the Dynamixel cable) connects to OV out on the DC-DC convertor and the "black" wire connects to GND. See wiring diagram, and note especially the keying on the Dynamixel cables.
     
      * Unfortunately you will have to use the connector keying to distinguish the ground and the signal cables since they are not actually colored or labelled in any way!
 
      * The "red" wire of the custom cable has 2 female connectors that should be attached to the second rocker switch. This rocker switch will control power supply to motors only, which will allow you to turn off or reset the motors, but keep the UP board powered. This is useful both to preserve battery life when you need to work on UP board configuration and programming, and to stop the motors if necessary without crashing the UP Board.
  
8. USB Connections

  Wiring 3 

  [_Drawing 9_: USB Connections](http://a360.co/2ajdTqA) ([USB Connection Diagram](http://a360.co/2ci6REp))

  * Connect RealSense R200 Camera to USB3 OTG port with the USB 3.0 cable provided in the camera kit.
     
  * Plug in USB2AX adapter into a (regular) USB2 port of the UP Board.

  * It is advisable to route camera and USB2AX cables in-between the Tower and UP Board. Address cable management and secure UP Board to the Tower plate with 4ea. M2.5x6 screws.
     
  * Insert Wi-Fi USB dongle into UP board.

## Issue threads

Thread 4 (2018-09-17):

unable to Launch the project with the "sawr/catkin_ws/src/sawr/sawr_master$ LAUNCH.md"

ShettyHarapanahalli, 2018-09-17:
Hi,

I am planning to use this package, I am able to make and install the package but when i try to launch the package i get a error.

DL:~/github/sawr/catkin_ws/src/sawr/sawr_master$ ./LAUNCH.md
./LAUNCH.md: line 1: syntax error near unexpected token `('
./LAUNCH.md: line 1: `Simple Autonomous Wheeled Robot (SAWR)'

Can you please help me fix this.

Regards,
SSH

mmccool, 2018-09-17:
This is an md, or MarkDown file.  It's documentation, not an executable.  Please look at it on github where it will be rendered properly: https://github.com/01org/sawr/blob/master/sawr_master/LAUNCH.md

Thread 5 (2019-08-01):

unable to install dynamixel sdk

aswinkumar2019, 2019-08-01:
Every step works fine except dynamixel installation.
I get the following error

root@aswin-desktop:~/Drivers/DynamixelSDK/c++/build/linux64# make
mkdir -p ./.objects/
g++ -O2 -O3 -DLINUX -D_GNU_SOURCE -Wall -c -I../../include/dynamixel_sdk -m64 -fPIC -g -c ../../src/dynamixel_sdk/group_bulk_read.cpp -o .objects/group_bulk_read.o
g++: error: unrecognized command line option ‘-m64’
Makefile:117: recipe for target '.objects/group_bulk_read.o' failed
make: *** [.objects/group_bulk_read.o] Error 1

Please help me to fix this error

aswinkumar2019, 2019-08-03:
Is this project actively developed?????

Closed 2019-11-30.

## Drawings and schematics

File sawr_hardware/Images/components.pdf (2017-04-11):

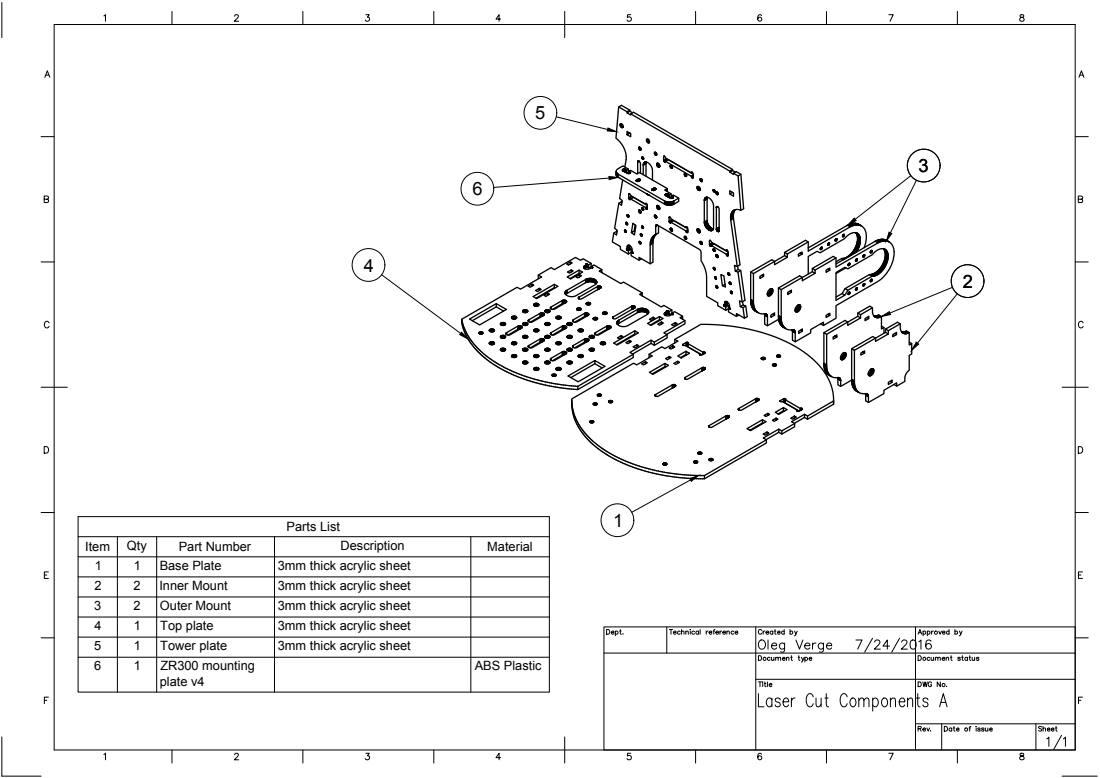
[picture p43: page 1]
Parts List

Item | Qty | Part Number | Description | Material
1 | 1 | Base Plate | 3mm thick acrylic sheet
2 | 2 | Inner Mount | 3mm thick acrylic sheet
3 | 2 | Outer Mount | 3mm thick acrylic sheet
4 | 1 | Top plate | 3mm thick acrylic sheet
5 | 1 | Tower plate | 3mm thick acrylic sheet
6 | 1 | ZR300 mounting plate v4 | | ABS Plastic

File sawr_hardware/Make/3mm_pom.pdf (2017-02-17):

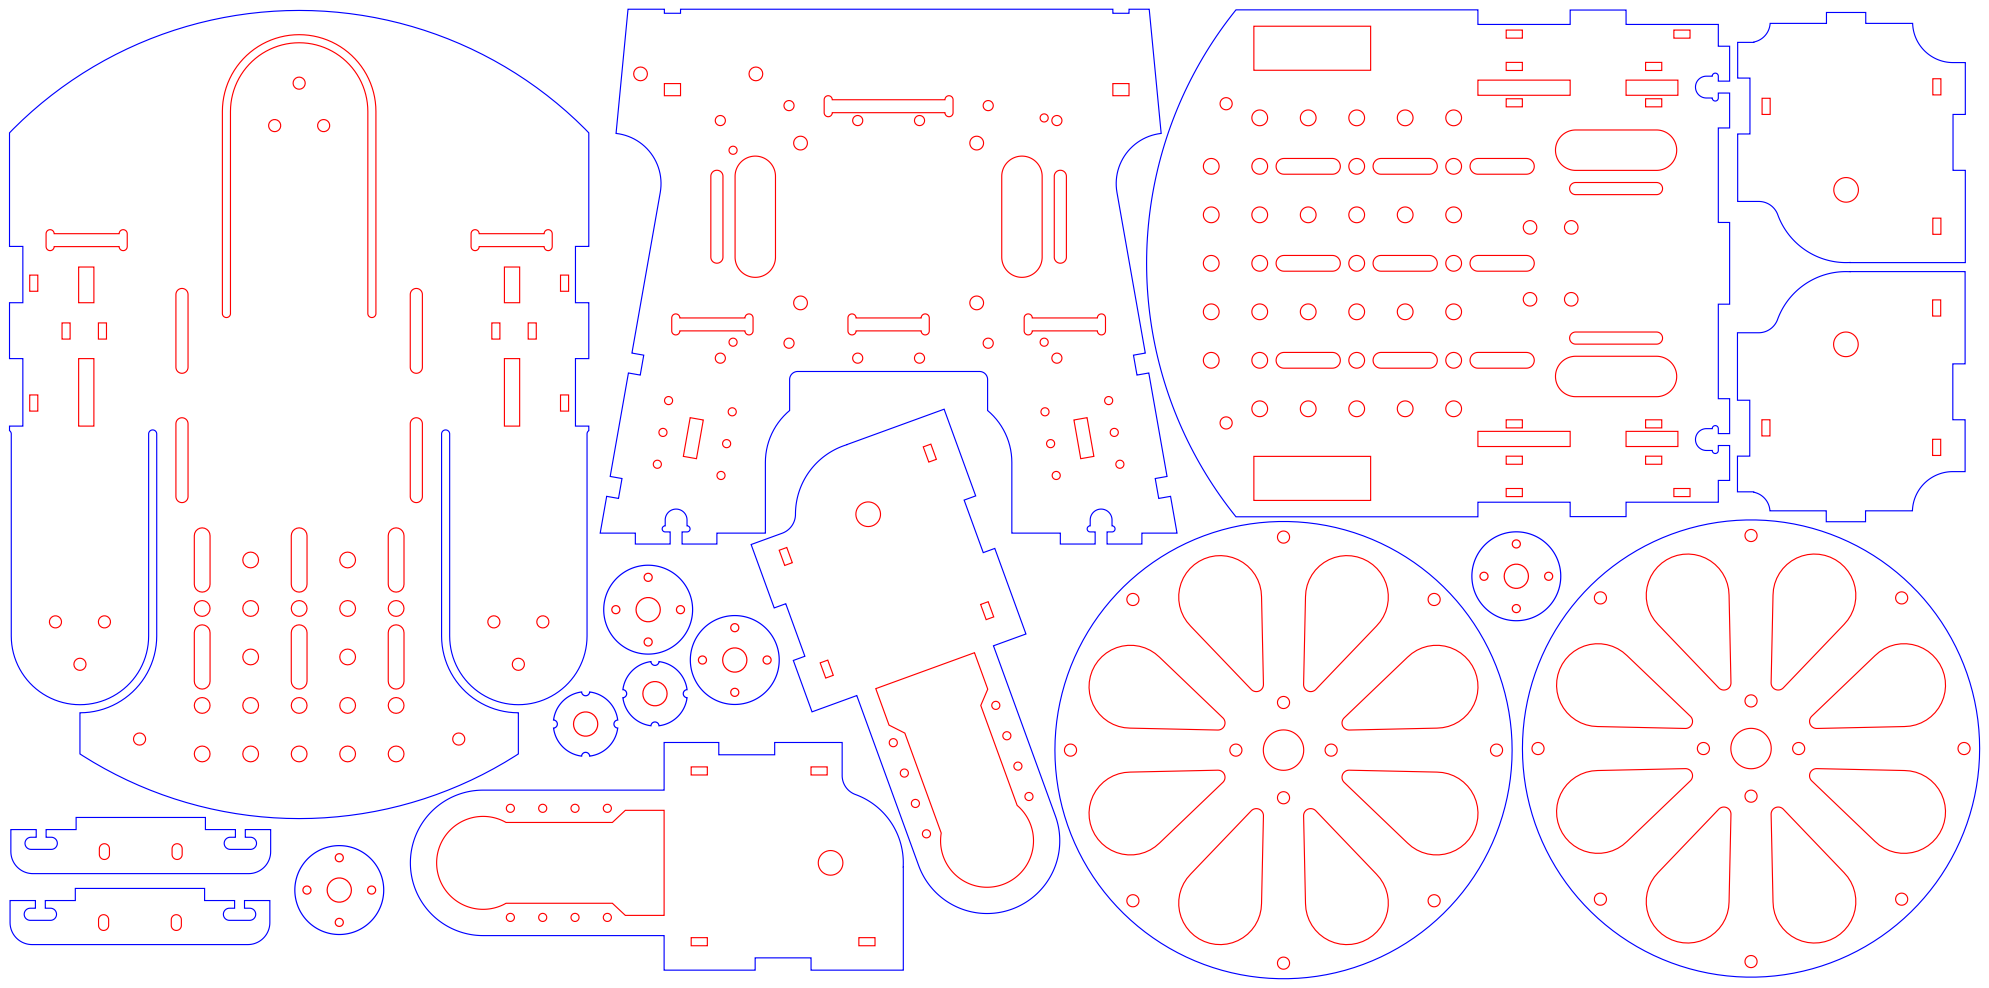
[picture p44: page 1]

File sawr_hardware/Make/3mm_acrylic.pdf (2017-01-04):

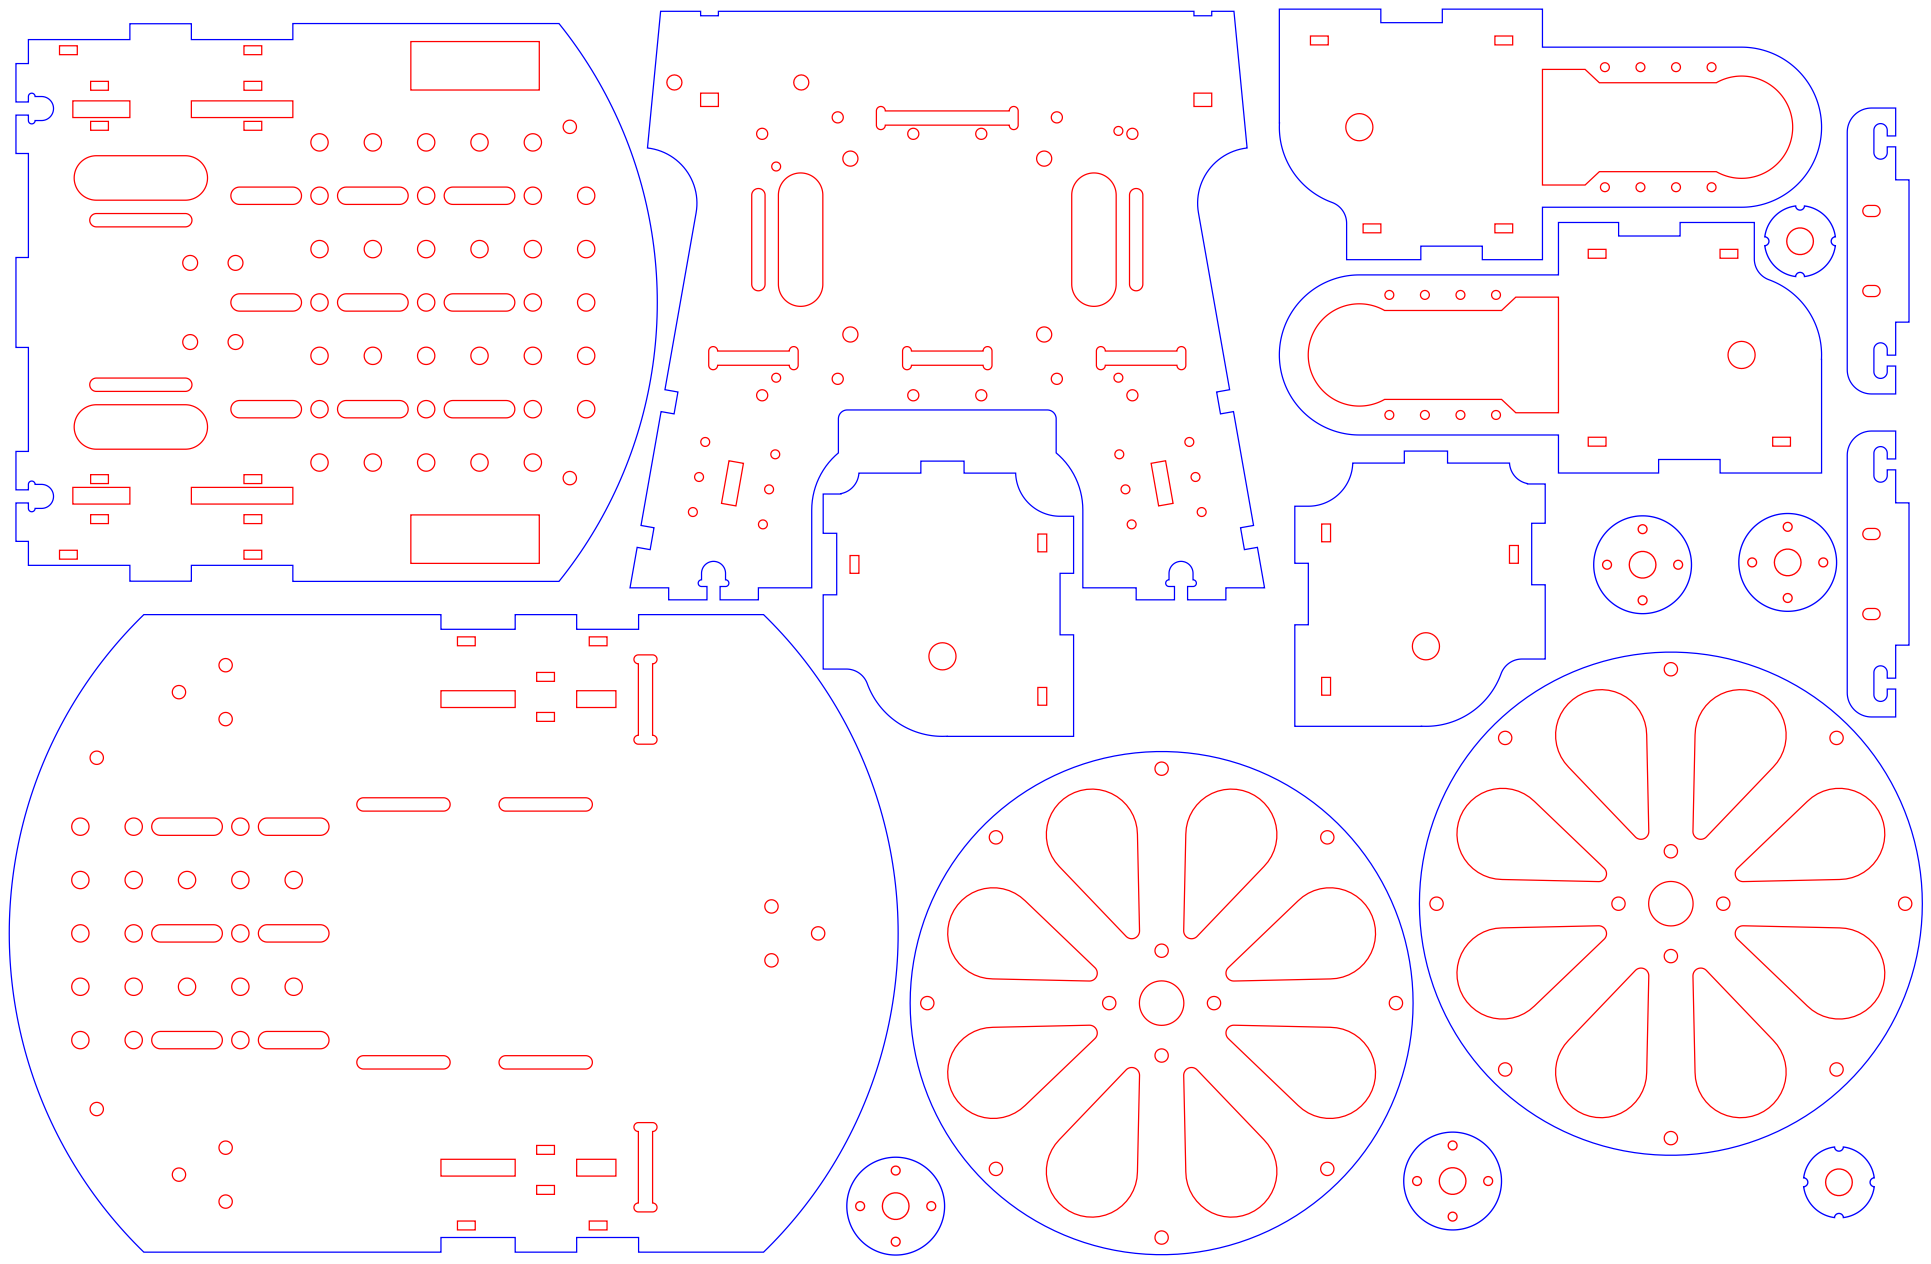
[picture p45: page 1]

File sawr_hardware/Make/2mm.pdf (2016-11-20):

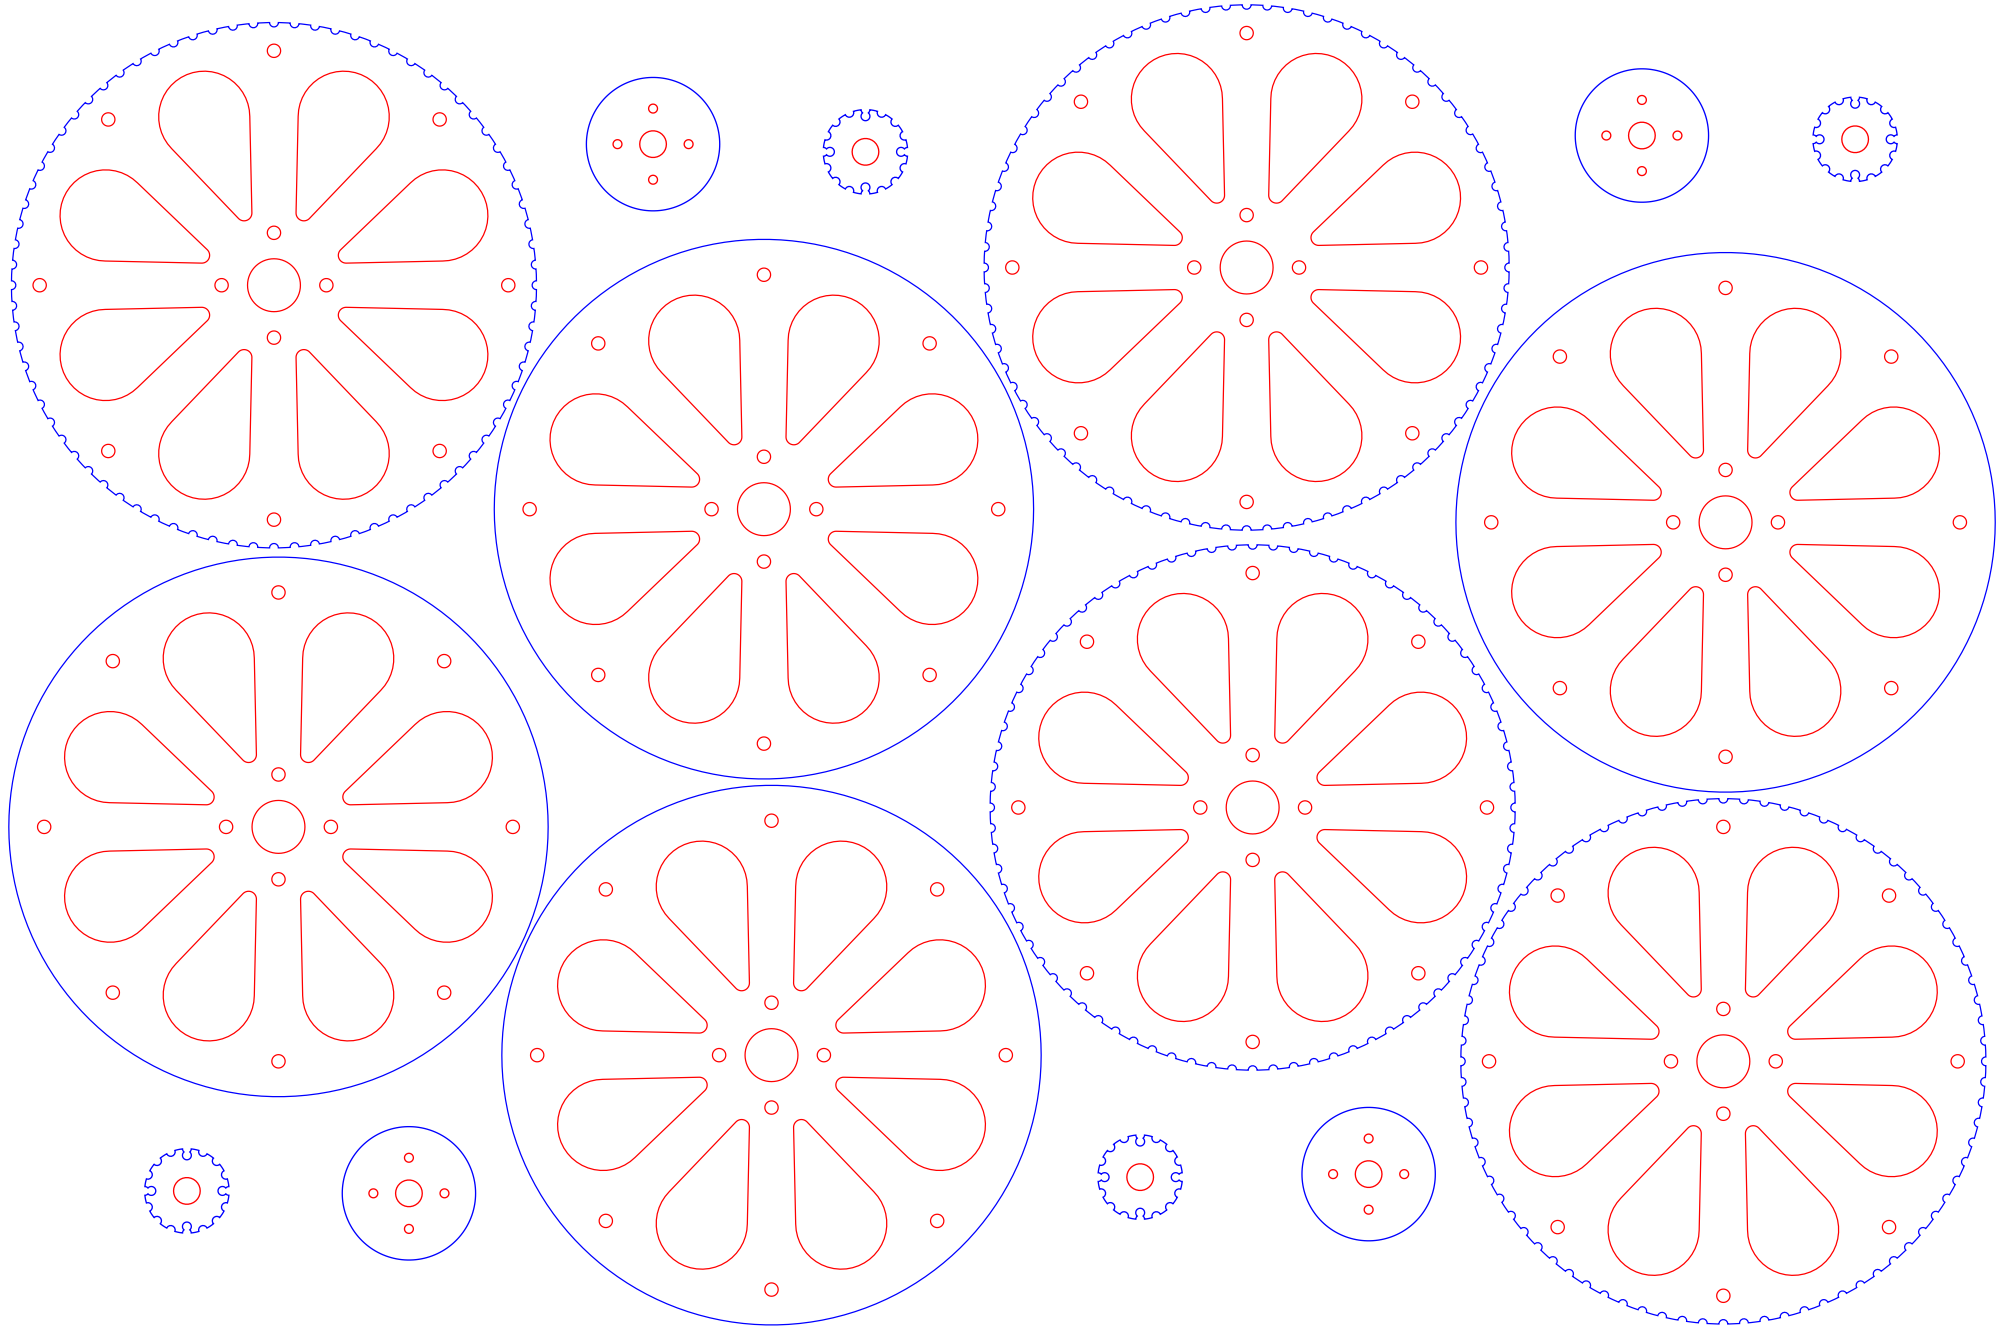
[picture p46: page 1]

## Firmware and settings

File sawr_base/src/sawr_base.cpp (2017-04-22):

/* 
 * Simple Autonomous Wheeled Robot (SAWR)
 * Motor Controller and Odometry  
 *
 * Motion platform controller using two Dynamixel MX-12W servos in "wheel" mode 
 * and a differential drive.
 *
 * Depends on the Dynamixel SDK for Linux and ROS.
 *
 * Author: Michael McCool, michael.mccool@intel.com
 * Copyright 2016 Intel Corporation
 * License: BSD-3, see LICENSE.md
 */
#include <math.h>
#include "ros/ros.h"
#include "std_msgs/String.h"
#include "geometry_msgs/Twist.h"
#include "std_msgs/Empty.h"
#include "geometry_msgs/Vector3.h"
#include "sensor_msgs/BatteryState.h"
#include "tf/transform_broadcaster.h"
#include "nav_msgs/Odometry.h"
#include "boost/lexical_cast.hpp"
#include <assert.h>

// header files for Dynamixel SDK
#include <unistd.h>
#include <fcntl.h>
#include <termios.h>
#include <stdlib.h>
#include <stdio.h>
#include "dynamixel_sdk.h"

// Dynamixel MX-12W control register addresses
const int dxl_mx12w_w_addr_cw_limit = 6; // word, RW, 0 for wheel mode
const int dxl_mx12w_w_addr_ccw_limit = 8; // word, RW, 0 for wheel mode
const int dxl_mx12w_w_addr_max_torque = 14; // word, RW
const int dxl_mx12w_b_addr_alarm_led = 17; // byte, RW
const int dxl_mx12w_b_addr_alarm_shutdown = 18; // byte, RW
const int dxl_mx12w_b_addr_torque_enable = 24; // byte, RW
const int dxl_mx12w_b_addr_led = 25; // byte, RW
const int dxl_mx12w_b_addr_gain_d = 26; // byte, RW
const int dxl_mx12w_b_addr_gain_i = 27; // byte, RW
const int dxl_mx12w_b_addr_gain_p = 28; // byte, RW
const int dxl_mx12w_w_addr_target_speed = 32;  // word, RW
const int dxl_mx12w_w_addr_torque_limit = 34;  // word, RW
const int dxl_mx12w_w_addr_speed = 38; // word, R
const int dxl_mx12w_w_addr_load = 40; // word, R
const int dxl_mx12w_b_addr_voltage = 42; // byte, R
const int dxl_mx12w_b_addr_temp = 43; // byte, R
const int dxl_mx12w_b_addr_moving = 46; // byte, R
const int dxl_mx12w_w_addr_punch = 48; // word, R
const int dxl_mx12w_b_addr_accel_limit = 73; // byte, R

// Maximum speed (Dynamixel servo limit), absolute value
int dxl_mx12w_max_speed = 1023;

// Maximum torque (Dynamixel servo limit)
int dxl_mx12w_max_torque = 1023;

// Maximum acceleration (Dynamixel servo limit)
int dxl_mx12w_max_accel = 255;

// Maximum punch (Dynamixel servo limit)
int dxl_mx12w_max_punch = 1023;

// Scale factor to multiply CPS (MX-12W register value) to get RPS
const double dxl_mx12w_cps_to_rps = (117.07/60.0)/1023.0;  // (r/s)/(c/s)

// Scale factor to multiple RPS to get CPS (MX-12W register value)
const double dxl_mx12w_rps_to_cps = 1023.0/(117.07/60.0);  // (c/s)/(r/s)

using namespace std;

// PARAMETERS
//   --> these should really be given in parameter files, perhaps with
//       support for dynamic updates, with documentation, etc.
//   --> param_ just indicates this is a parameter, external name in YAML file
//       (when supported) should drop prefix
// TODO: Support reading these from parameter server

// After this many seconds, if no new commands, motors will automatically stop (s)
double param_motor_timeout = 1.0;  
// How often odometry is polled and integrated (Hz)
double param_polling_rate = 100.0;    
// Odometry is published on every nth polling loop
int param_odom_publication_divisor = 10;           
// Battery state is published on every nth polling loop
int param_batt_publication_divisor = 10000;           
// Dynamixel ID for left motor (when facing towards the front of the robot)
int param_left_motor_id = 1;       
// Dynamixel ID for right motor (when facing towards the front of the robot)
int param_right_motor_id = 2;      
// Mechanical advantage of transmission
double param_mech = 6.21882;
// Dynamixel baudrate
int param_baudrate = 1000000;
// Dynamixel serial port device
//char param_device[] = "/dev/ttyUSB0"; // for USB2Dynamixel
char param_device[] = "/dev/ttyACM0";  // for USB2AX
// Tire diameter - minor radius (m)
// double param_tire_diameter = 6.89/1000.0; // mm -> m
double param_tire_diameter = 5.7/1000.0; // mm -> m
// Tire ID - inner diameter (assuming no belt drive)
double param_tire_id = 114.6;
// Diameter of wheels (m) on the outside of tires
double param_wheel_diameter = 125.815/1000.0;  // mm -> m
// Distance between wheel-ground contact points (m)
double param_wheel_base = 181.0/1000.0;  // mm -> m 
// Wheel dihedral angle (degrees; positive is inwards at top)
double param_dihedral = 10;
// P parameter for PID controller (Dynamixel units)
int param_gain_p = 8;
// I parameter for PID controller (Dynamixel units)
int param_gain_i = 0;
// D parameter for PID controller (Dynamixel units)
int param_gain_d = 8;
// Maximum motor velocity (in Dynamixel units; desired, not servo limit)
int param_max_speed = dxl_mx12w_max_speed/4; // it's not a race, avoid smashups
// Maximum motor acceleration (in Dynamixel units; desired, not servo limit))
int param_max_accel = dxl_mx12w_max_accel/8; // avoid being too jerky
// Maximum motor torque (in Dynamixel units; desired, not servo limit))
int param_max_torque = dxl_mx12w_max_torque; // can use all we can get!
// Maximum motor punch (in Dynamixel units; desired, not servo limit))
int param_max_punch = 0; // dxl_mx12w_max_punch/4; 

// DERIVED VALUES
// --> If/when YAML and/or dynamic parameter updates are supported these will have to be
//     recomputed as needed at runtime, which is why they (and the parameters above) are not
//     marked as const.

// Effective wheel diameter (taking into account dihedral angle on wheel and tire)
double effective_wheel_diameter = 
   param_wheel_diameter*cos(2*M_PI*param_dihedral)
   - 2*param_tire_diameter*(1.0-cos(2*M_PI*param_dihedral));
// Wheel circumference (m per revolution)
double wheel_circumference = M_PI*param_wheel_diameter;   
// Effective wheel circumference (m per revolution)
double effective_wheel_circumference = M_PI*effective_wheel_diameter;   
// Base circumference
double base_circumference = M_PI*param_wheel_base;

// Calibration
//double param_calibration = 0.6;
//double param_calibration = 0.65;
//double param_calibration = 0.7;
double param_calibration = 0.8;
//double param_calibration = 0.9;
//double param_calibration = 1.0;
//double param_calibration = 1.1;

// Amount to scale linear speed values in m/s to get motor speeds in cps
                                                           // -> c/s
double linear_scale = dxl_mx12w_rps_to_cps                 // (c/s)/(r/s)
                    * param_calibration                   //   = c/r
                    * (32.0/254.0)                         // W/A gear ratio
                    * param_mech                           // mechanical advantage of transmission
                    * (1.0/effective_wheel_circumference); // r/m
                                                           // <- m/s
// Amount to scale w values in twist (rad/s) to get motor speeds in cps 
double angular_scale = linear_scale                        //   m/s -> c/s
                     * base_circumference                  // m/R (R = base rev)
                     / (2.0*M_PI);                         // R/rad
                                                           // <- rad/s

// Scales for odom input (in case different from speed targets)
double odom_linear_scale = linear_scale;
double odom_angular_scale = angular_scale;

#include <signal.h>

// Signal handler; need to catch and handle signals to clean up 
// semi-gracefully
int running = 1;
void sig_handler(int signo) {
    if (signo == SIGINT) {
        running = 0;
    }
}
void register_sig_handler() {
    signal(SIGINT, sig_handler);
}

dynamixel::PortHandler *portHandler = 0; 
dynamixel::PacketHandler *packetHandler = 0;

// number of times to repeat a failed command
const int num_tries = 5;

// Dynamixel helper functions
bool motor_write_byte(int id, int addr, unsigned int value) {
    bool success = true;
    assert(0 != packetHandler);
    assert(0 != portHandler);
    uint8_t er;  
    int cr = packetHandler->write1ByteTxRx(
        portHandler, id, 
        addr, uint8_t(0xFF & value), 
        &er
    );
    if (COMM_SUCCESS != cr) {
        // TODO: should send these as strings to ROS logger
        packetHandler->printTxRxResult(cr);
        success = false;
    } else if (0 != er) {
        // TODO: should send these as strings to ROS logger
        packetHandler->printRxPacketError(er);
        success = false;
    }
    return success;
}
bool motor_write_word(int id, int addr, unsigned int value) {
    bool success = true;
    assert(0 != packetHandler);
    assert(0 != portHandler);
    uint8_t er;  
    int cr = packetHandler->write2ByteTxRx(
        portHandler, id, 
        addr, uint16_t(0xFFFF & value), 
        &er
    );
    if (COMM_SUCCESS != cr) {
        // TODO: should send these as strings to ROS logger
        packetHandler->printTxRxResult(cr);
        success = false;
    } else if (0 != er) {
        // TODO: should send these as strings to ROS logger
        packetHandler->printRxPacketError(er);
        success = false;
    }
    return success;
}
bool motor_read_byte(int id, int addr, unsigned int *value) {
    bool success = true;
    assert(0 != packetHandler);
    assert(0 != portHandler);
    uint8_t v;
    uint8_t er;  
    int cr = packetHandler->read1ByteTxRx(
      portHandler, id, 
      addr, &v, 
      &er
    );
    if (COMM_SUCCESS != cr) {
      // TODO: should send these as strings to ROS logger
      packetHandler->printTxRxResult(cr);
      success = false;
    } else if (0 != er) {
      // TODO: should send these as strings to ROS logger
      packetHandler->printRxPacketError(er);
      success = false;
    }
    *value = (unsigned int)(v);
    return success;
}
bool motor_read_word(int id, int addr, unsigned int *value) {
    bool success = true;
    assert(0 != packetHandler);
    assert(0 != portHandler);
    uint16_t v;
    uint8_t er;  
    int cr = packetHandler->read2ByteTxRx(
      portHandler, id, 
      addr, &v, 
      &er
    );
    if (COMM_SUCCESS != cr) {
      // TODO: should send these as strings to ROS logger
      packetHandler->printTxRxResult(cr);
      success = false;
    } else if (0 != er) {
      // TODO: should send these as strings to ROS logger
      packetHandler->printRxPacketError(er);
      success = false;
    }
    *value = (unsigned int)(v);
    return success;
}

// Enable (or disable) motor torque
bool motor_enable(int id, unsigned int en = 1) {
    bool success = true;
    int tries = num_tries;
    while (!motor_write_byte(id,dxl_mx12w_b_addr_torque_enable,en)) {
      if (0 == --tries) {
        success = false;
        break;
      }
    }
    return success; 
}
bool motor_disable(int id) {
    return motor_enable(id,0);
}
// Set wheel mode
bool motor_set_wheel_mode(int id) {
    bool success = true;
    int tries = 5;
    while (!motor_write_word(id,dxl_mx12w_w_addr_cw_limit,0) ||
           !motor_write_word(id,dxl_mx12w_w_addr_ccw_limit,0) 
    ) {
      if (0 == --tries) {
        success = false;
        break;
      }
    }
    return success; 
}
// Set torque limit
bool motor_set_max_torque(int id, unsigned int torque) {
    bool success = true;
    int tries = num_tries;
    while (!motor_write_word(id,dxl_mx12w_w_addr_torque_limit,torque)) {
      if (0 == --tries) {
        success = false;
        break;
      }
    }
    return success; 
}
// Set accleration limit
bool motor_set_max_accel(int id, unsigned int accel) {
    bool success = true;
    int tries = num_tries;
    while (!motor_write_byte(id,dxl_mx12w_b_addr_accel_limit,accel)) {
      if (0 == --tries) {
        success = false;
        break;
      }
    }
    return success; 
}
// Set punch limit
bool motor_set_max_punch(int id, unsigned int punch) {
    bool success = true;
    int tries = num_tries;
    while (!motor_write_word(id,dxl_mx12w_w_addr_punch,punch)) {
      if (0 == --tries) {
        success = false;
        break;
      }
    }
    return success; 
}
// Set PID parameters
bool motor_set_pid(int id, unsigned int p, unsigned int i, unsigned int d) {
    bool success = true;
    int tries = 5;
    while (!motor_write_byte(id,dxl_mx12w_b_addr_gain_p,p) || 
           !motor_write_byte(id,dxl_mx12w_b_addr_gain_i,i) || 
           !motor_write_byte(id,dxl_mx12w_b_addr_gain_d,d)
    ) {
      if (0 == --tries) {
        success = false;
        break;
      }
    }
    return success; 
}
// Set target speed (using cpr units, but signed; + is CCW rotation)
// also clamps speed to capability of servo
bool motor_set_target_speed(int id, double value) {
    int speed = int(round(value));
    if (speed < 0) {
      speed = dxl_mx12w_max_speed - speed + 1; // this is actually an addition
      if (speed > 2*dxl_mx12w_max_speed) speed = 2*dxl_mx12w_max_speed;
    } else {
      if (speed >= dxl_mx12w_max_speed) speed = dxl_mx12w_max_speed;
    }
    bool success = true;
    int tries = num_tries;
    // ROS_INFO_STREAM("servo "<<id<<" target: "<<value<<"->"<<speed);
    while (!motor_write_word(id,dxl_mx12w_w_addr_target_speed,speed)) {
      if (0 == --tries) {
        success = false;
        break;
      }
    }
    return success; 
}
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
int main (
    int argc, 
    char** argv
) {
    // ROS init
    ros::init(argc, argv, "sawr_base");  //node_name
    ros::NodeHandle nh;
    ROS_INFO_STREAM("sawr_base started");

    // DXL init
    portHandler = dynamixel::PortHandler::getPortHandler(param_device);
    packetHandler = dynamixel::PacketHandler::getPacketHandler(1.0);

    // Set communications rate (motors should be configured in advance to match)
    portHandler->setBaudRate(param_baudrate);

    // Set to Wheel mode
    // TODO: deal with case that calls fail, at least by sending out ROS error message
    (void)motor_set_wheel_mode(param_left_motor_id);
    (void)motor_set_wheel_mode(param_right_motor_id);

    // Set max torque
    // TODO: deal with case that calls fail, at least by sending out ROS error message
    (void)motor_set_max_torque(param_left_motor_id,param_max_torque);
    (void)motor_set_max_torque(param_right_motor_id,param_max_torque);

    // Set max accel
    // TODO: deal with case that calls fail, at least by sending out ROS error message
    (void)motor_set_max_accel(param_left_motor_id,param_max_accel);
    (void)motor_set_max_accel(param_right_motor_id,param_max_accel);

    // Set PID parameters
    // TODO: deal with case that calls fail, at least by sending out ROS error message
    (void)motor_set_pid(param_left_motor_id,param_gain_p,param_gain_i,param_gain_d);
    (void)motor_set_pid(param_right_motor_id,param_gain_p,param_gain_i,param_gain_d);

    // Set initial target speed to zero
    // TODO: deal with case that calls fail, at least by sending out ROS error message
    (void)motor_set_target_speed(param_left_motor_id,0);
    (void)motor_set_target_speed(param_right_motor_id,0);

    // Enable DXL Torque on both motors
    // TODO: deal with case that calls fail, at least by sending out ROS error message
    (void)motor_enable(param_left_motor_id);
    (void)motor_enable(param_right_motor_id);

    // Arrange to exit cleanly 
    register_sig_handler(); 

    // PUBLISHERS

    // Create tf broadcaster for odom frame
    odom_broadcaster = new tf::TransformBroadcaster();

    // Publish "odom" topic 
    odom_pub = new ros::Publisher(nh.advertise<nav_msgs::Odometry>(
        "odom", 
        100          // queue size
    ));     

    // Publish "battery_state" topic 
    batt_pub = new ros::Publisher(nh.advertise<sensor_msgs::BatteryState>(
        "battery_state", 
        100          // queue size
    ));     
    // initialize template
    sensor_msgs::BatteryState batt_msg;
    batt_msg.present = true;
    batt_msg.location = "0";
    batt_msg.serial_number = "none";
    batt_msg.power_supply_health = sensor_msgs::BatteryState::POWER_SUPPLY_HEALTH_UNKNOWN;
    batt_msg.power_supply_status = sensor_msgs::BatteryState::POWER_SUPPLY_STATUS_UNKNOWN;
    batt_msg.power_supply_technology = sensor_msgs::BatteryState::POWER_SUPPLY_TECHNOLOGY_LIPO;

    // SUBSCRIBERS

    // Subscribe to *cmd_vel "Twist" topics 
    //   => these both use the same callback.  
    //   => we do not do any prioritization (yet)
    cmd_vel_sub = new ros::Subscriber(nh.subscribe<geometry_msgs::Twist>(
        "cmd_vel", 
        100,         // queue size  
        &twist_callback
    ));
    nav_cmd_vel_sub = new ros::Subscriber(nh.subscribe<geometry_msgs::Twist>(
        "nav_cmd_vel", 
        100,         // queue size  
        &twist_callback
    ));

    // TODO: should really make sure none of the above calls return errors 

    // Get starting timestamp
    ros::Time current_time, last_time;
    last_time = ros::Time::now();
    current_time = ros::Time::now(); // TODO: wait until this is not 0

    // Pretend we just got a twist event to avoid immediate timeout
    last_twist_event_time = current_time;

    // Integration variables for odometry
    double x = 0.0;
    double y = 0.0;
    double w = 0.0;

    // Spin and wait for stuff to come in
    ros::Rate r(param_polling_rate); 
    int odom_publication_counter = param_odom_publication_divisor;
    int batt_publication_counter = param_batt_publication_divisor;
    while (ros::ok() && running) {
        // yield to ROS once per cycle
        ros::spinOnce();

        // keep track of iterations
        odom_publication_counter--;
        batt_publication_counter--;

        // Grab new timestamp
        ros::Time current_time = ros::Time::now();
        // Compute time difference
        double dt = (current_time - last_time).toSec();

        // MOTOR CONTROL TIMEOUT

        // Stop motors if motor timeout has expired.  This
        // prevents the motors running forever if communication is lost.
        if (motor_timer_active &&
            (current_time.toSec() > last_twist_event_time.toSec() + param_motor_timeout)) {
          motor_timer_active = false;
          motor_set_target_speed(param_left_motor_id,0.0);
          motor_set_target_speed(param_right_motor_id,0.0);
          ROS_INFO_STREAM("motor command timeout"); // a warning instead?

          // To avoid doing this every time around the polling loop for 
          // no reason, reset timer, as if this were an actual command.
          // ideally we would just check if the input command queue is empty, but...
          last_twist_event_time = current_time;
        }

        // ODOMETRY 

        // Get current (measured, actual) speed from each motor
        // TODO: deal with case that calls fail, at least by sending out ROS error message
        double s1, s2;
        (void)motor_get_speed(param_left_motor_id,&s1);
        (void)motor_get_speed(param_right_motor_id,&s2);

        // Transform into linear and angular speeds in m/s and rad/s
        double vw = -0.5*(s1 + s2);
        double vx =  0.5*(s1 - s2);
        vx /= odom_linear_scale;
        vw /= odom_angular_scale;

        // Print velocity *occasionally*, if it is non-zero, for debug purposes
        if (0 == odom_publication_counter) {
            if (abs(vx) + abs(vw) > 0) {
                ROS_INFO_STREAM("base vel ["<<s1<<","<<s2<<"] -> ("<<vx<<";"<<vw<<") over "<<dt<<"s");
            }
        }

        // Integrate odometry
        //   Differential drive, so vy always zero in local frame.
        //   However, velocity needs to be rotated by current orientation to 
        //   map into odometry frame.
        double dx = cos(w)*vx*dt;
        double dy = sin(w)*vx*dt;
        double dw = vw*dt;
        x += dx;
        y += dy;
        w += dw;

        // Output odometry at decimated rate
        if (0 == odom_publication_counter) {
            odom_publication_counter = param_odom_publication_divisor; 

            // Print updated odom pose (if it changes), for debug purposes
            if (abs(vx) + abs(vw) > 0) {
               ROS_INFO_STREAM("odom pose (" << x << "," << y << ";" << w << ")");
            }
 
            // All odometry is 6DOF so need a quaternion created from yaw
            geometry_msgs::Quaternion odom_quat =
                tf::createQuaternionMsgFromYaw(w);
 
            // Create an odometry message 
            nav_msgs::Odometry odom;
            odom.header.stamp = current_time;
            odom.header.frame_id = "odom";
            //odom.child_frame_id = "base_footprint";
 
            // Set the accumulated pose as a 3D (6DOF) value
            odom.pose.pose.position.x = x;
            odom.pose.pose.position.y = y;
            odom.pose.pose.position.z = 0.0;
            odom.pose.pose.orientation = odom_quat;

            // Set the velocity as a twist relative to the child frame
            odom.twist.twist.linear.x = vx;
            odom.twist.twist.linear.y = 0;
            odom.twist.twist.angular.z = vw;

            // Publish odom message 
            odom_pub->publish(odom);

            // Echo header data from odom message to odom transform header
            geometry_msgs::TransformStamped odom_trans;
            odom_trans.header.stamp = odom.header.stamp; 
            odom_trans.header.frame_id = odom.header.frame_id; 
            odom_trans.child_frame_id = "base_footprint";
 
            // Echo pose data from odom message to odom transform
            odom_trans.transform.translation.x = odom.pose.pose.position.x;
            odom_trans.transform.translation.y = odom.pose.pose.position.y;
            odom_trans.transform.translation.z = odom.pose.pose.position.z;
            odom_trans.transform.rotation = odom.pose.pose.orientation;
 
            // Broadcast the odom transform  
            odom_broadcaster->sendTransform(odom_trans);
        }

        // Output battery state at decimated rate
        if (0 == batt_publication_counter) {
            batt_publication_counter = param_batt_publication_divisor;
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

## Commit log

2016-04-01 Initial commit of fetchbot builds no errors
    [fetchbot.urdf, fetchbot.urdf.xacro, r200.urdf.xacro]
2016-06-13 fixedfixed planner performance issue
    [default.cfg, median.cfg, minimal.cfg]
2016-07-22 modified to run Whr
    [r200.urdf.xacro, whr.urdf, whr.urdf.xacro]
2016-09-05 rename fetchbot to whr, consolidate files
    [default.cfg, fetchbot.urdf, fetchbot.urdf.xacro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]
2016-09-06 port to Joule and Kinetic. R200@30fps, xacro fixes
    [whr.urdf.xacro]
2016-11-20 Add CAD files and BOM for robot hardware
    [base.dxf, bom.xlsx, driver.dxf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]
2016-11-20 change axle hole dimensions and spacer size
    [whr_bot.scad]
2016-11-30 Added latest BOM in xlsx and csv format
    Added latest BOM in xlsx and csv format
    [Parts list for Whr configuration with UP board (RDK)_v2.csv, Parts list for Whr configuration with UP board (RDK)_v2.xlsx]
2016-11-30 removed old bom
    removed old bom
    [bom.xlsx]
2016-11-30 Added Mechanical and Electrical assembly Instructions
    Added Mechanical and Electrical assembly Instructions in pdf format
2016-12-01 renamed files to make it shorter
    [BOM_RDK_v2.csv, BOM_RDK_v2.xlsx]
2016-12-01 Adding self made stls for braket, servo, switch
2016-12-10 Change name from Whr to SAWhR
    [BOM_RDK_v2.csv, BOM_RDK_v2.xlsx, base.dxf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]
2016-12-17 Name change to "SAWR". Not yet tested.
    [BOM_RDK.csv, BOM_RDK_v2.xlsx, base.dxf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]
2016-12-17 Factor out r200 model, add zr300 model
    [frame.scad, r200.scad, zr300.scad]
2016-12-22 update frame design with mount for zr300
    [frame.scad, zr300.scad, zr300_params.scad]
2016-12-26 cleanup in OpenSCAD files; modular nuts and bolts
    [bolt_params.scad, bolts.scad, frame.scad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]
2016-12-26 Update frame to use bolt modules
    [frame.scad]
2016-12-26 add strain-relief slots for cables ties to zr300 mount
    [frame.scad, r200.scad, r200_params.scad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]
2016-12-28 add up squared support; improve robustness with acrylic
    [base.dxf, driver.dxf, driver_mount.dxf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]
2016-12-29 correct dimensions for up squared; add accessory grid (turned off by default)
    [frame.scad, zr300.scad]
2016-12-30 fix smoothness controls, cut_t spacing on T-slots
    [base.dxf, base_accessory.dxf, bolt_params.scad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]
2017-01-04 clean up cut and part files for latest frame
    [base.dxf, base_accessory.dxf, frame.scad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]
2017-02-03 tweak default smoothness settings
    [smooth_make.scad]
2017-02-03 Clean up HW folder
    Updated BOM links to RDK, minor updates in assembly instructions,
    updated ros-fetchbot/sawr_description/hardware/Modules/External/ - all
    propriatery STLs replaced with self made stls
    [BOM_RDK_v2.csv, BOM_RDK_v2.xlsx]
2017-02-03 updated servo.stl
    Mofified servo.stl, which had to be scaled and rotated to fit properly
    in frame.scad
2017-02-17 add pom versions of cut files, mod wheel_potrude
    [base_accessory.dxf, frame.scad]
2017-02-21 clean up names for instructions and BOM
    [BOM_RDK.csv, BOM_RDK.xlsx]
2017-03-09 Upload UP.stl
    Upload UP.stl
    [frame.scad]
2017-03-17 update version and URLs in BOM and instructions
2017-04-06 Update README.md
    Add link to assembly instructions
2017-04-06 Update README.md
    fix link to Assembly/INSTRUCTIONS.md
2017-04-06 Update README.md
    Add a bunch of hyperlinks to Joule, RealSense, UP Board, etc.
2017-04-06 Update INSTRUCTIONS.md
    change links for tower diagram and wheel diagram
2017-04-06 Add files via upload
    upload wheel_diag
2017-04-06 fix scale/translation issue with replacement UP
    [frame.scad]
2017-04-06 Update bolt_params.scad
    update copyright to 2017
    [bolt_params.scad]
2017-04-07 Update wiring_2.png
    fix spelling mistake: Dynamyxel -> Dynamixel
2017-04-10 reorg hardware package... partial
    [BOM_RDK.csv, BOM_RDK.xlsx, base.dxf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]
2017-04-10 clean up BOM, use only one file (CSV)
    [BOM_RDK.csv, BOM_RDK.xlsx]
2017-04-10 Update README.md
    fix links to reorganized HW and assembly instructions
2017-04-10 Update ASSEMBLY.md
    spelling fix
2017-04-11 Add images for laser-cut components for frame
    local files for laser-cut components for frame to make assembly instructions more self-contained
2017-04-11 Section headers and images
    Add an image of a real SAWR and some section headers to make content easier to navigate. Remove some of the unnecessary verbiage in the additional materials section
2017-04-11 Update ASSEMBLY.md
    Remove laser cut details
2017-04-11 Update README.md
    Put all the instructions for how to cut sheets in one place.
2017-04-11 Update README.md
    Remove details of use of laser cut files (now covered in Make/README.md)
2017-04-12 Update ASSEMBLY.md
    Add more info on batteries
2017-04-12 Update ASSEMBLY.md
    Fix formatting
2017-04-12 Update ASSEMBLY.md
    add more battery advice
2017-04-17 Update INSTALL.md
    Fix things, lmess up section in UP WiFi drivers, no Undo... argh
2017-04-22 tweak calibration data for motion
2017-09-12 add script for powersave gvnr
2018-05-29 Doc updates for UP Board and RealSense
    A few doc changes to address some bitrot:
    1. The current version of librealsense no longer supports the R200 or ZR300. Give instructions on how to check out the legacy version.
    2. Add note about LD_LIBRARY_PATH (ROS seems to clobber /usr/local/lib)
    3. Update instructions for installing the Aaeon kernel on the UP board
2018-05-29 Need kinetic-devel branch of Dynamixel SDK
    Document the need to explicitly check out the kinetic-devel version of the Dynamixel SDK to ensure dxl_monitor works, as it uses some functions (print*) that are deprecated and omitted from the lates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
